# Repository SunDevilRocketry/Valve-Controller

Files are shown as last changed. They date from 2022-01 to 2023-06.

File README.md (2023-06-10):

<h1>Valve Controller</h1>

<p>PCB Revision: 3.1</p>
<p>PCB Part No: L0005</p>
<p>The liquid engine's valve controller (L0005) contains the processor responsible for managing valve actuation commands issued by the liquid engine controller (L0002). The board contains opto-isolated solid state relays for solenoid actuation and a Pulse Width Modulation interface for issuing stepper motor commands that initiate actuation of the liquid engine's main propellant valves. The board contains an STM32H7 ARM Cortex-M7 microcontroller for processing, programmed using an STLink/V2 with a 20-pin IDC cable connection. The board is powered from the 5V buck converter on L0002, which is also used to power the photogate sensors used for valve position calibration. In order to allow the controller to know the true actuation state of the solenoids even in the event of a power failure, the board contains an AC power supply monitoring circuit which produces an indication signal read by the MCU when AC power is available for solenoid actuation. </p>

<p><b>Working Directory Structure:</b></p>

<p>
   cad: 3d models

   doc: documentation

   img: images of circuit/footprints for github display 

   lib: libraries for schematic symbols and footprints

   production: files needed for pcb fabrication, e.g. gerbers, profile, drill file

   sim: simulation models/files 

   src: source design files, e.g. schematic and PCB layout files
</p>

<h2>3D Model: </h2>
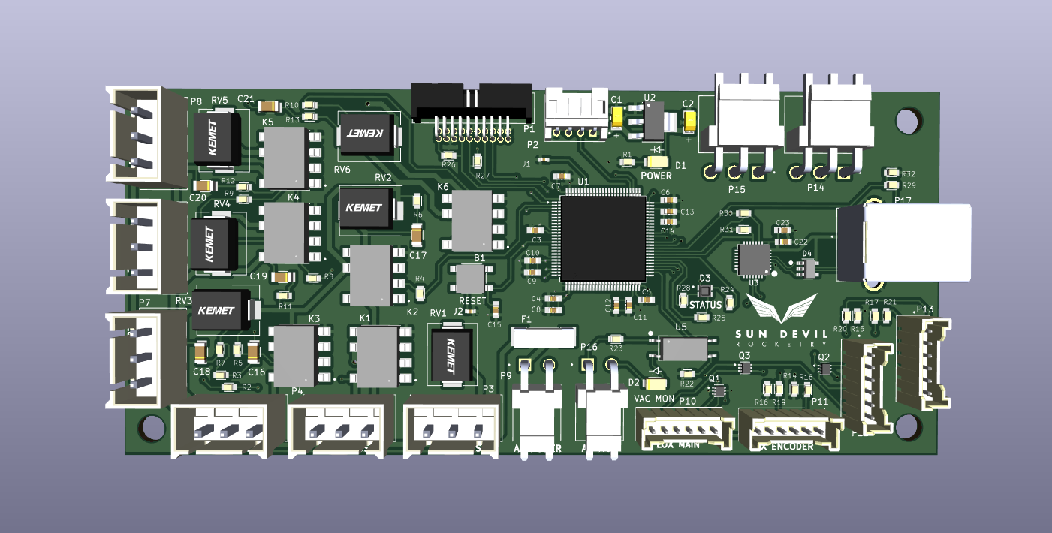
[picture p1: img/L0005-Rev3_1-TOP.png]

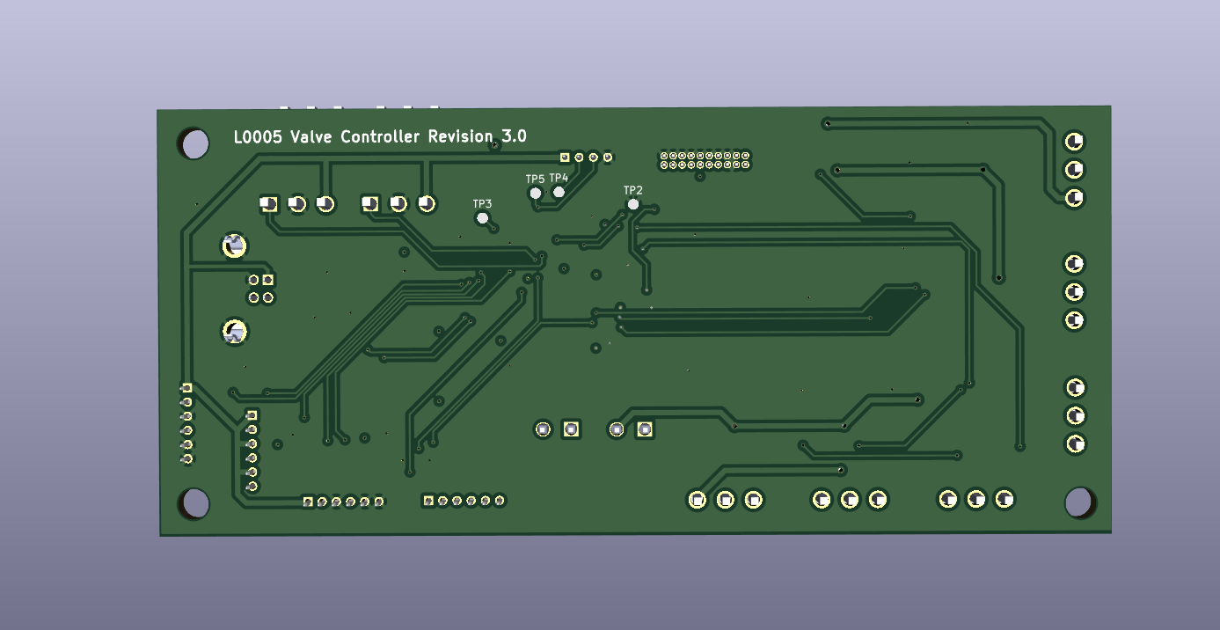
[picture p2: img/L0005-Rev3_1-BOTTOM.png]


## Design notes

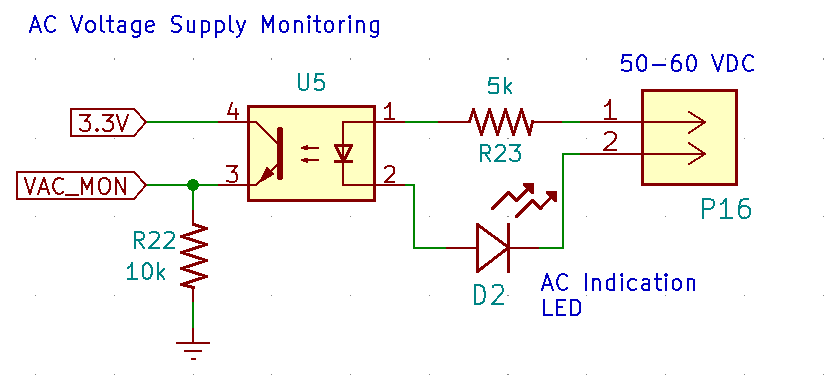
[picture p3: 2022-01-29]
img/AC-Supply-Monitoring-schematic.png

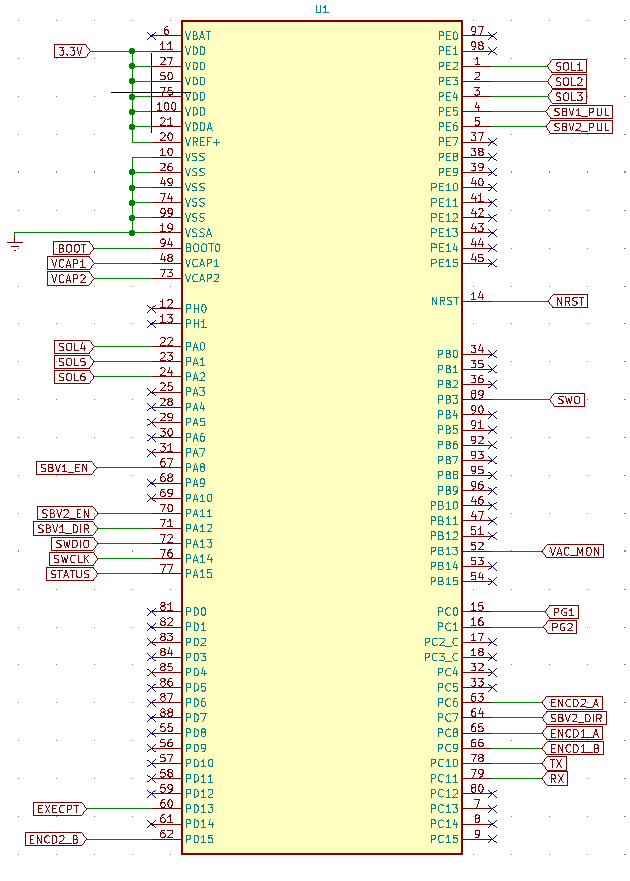
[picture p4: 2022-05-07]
img/MCU-schematic.png

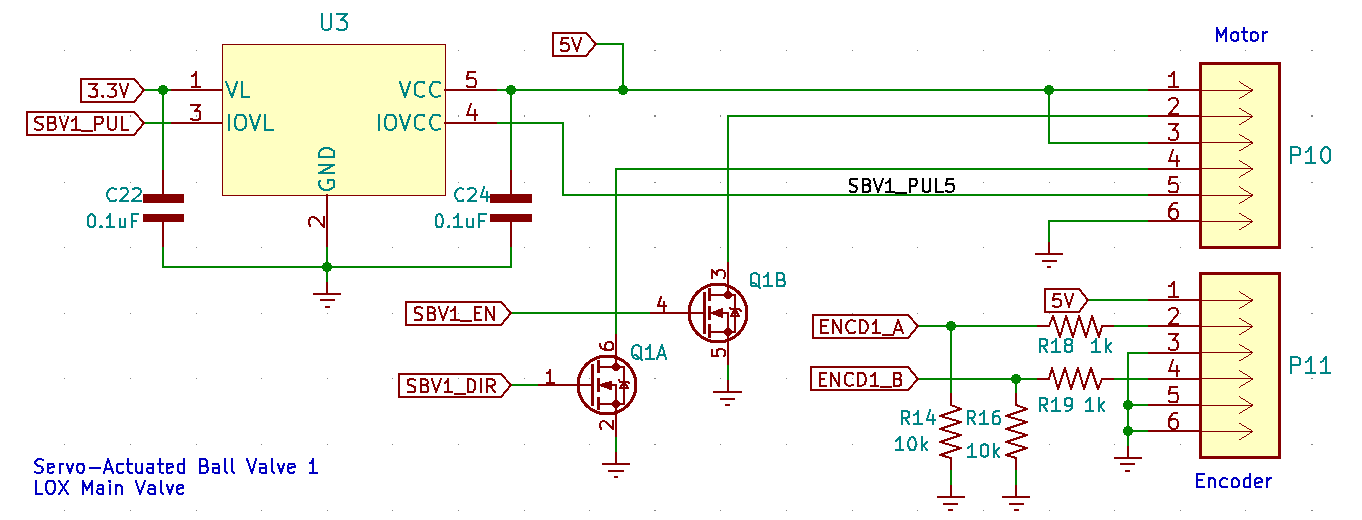
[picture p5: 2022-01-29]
img/Ball-Valve-Schematic.png

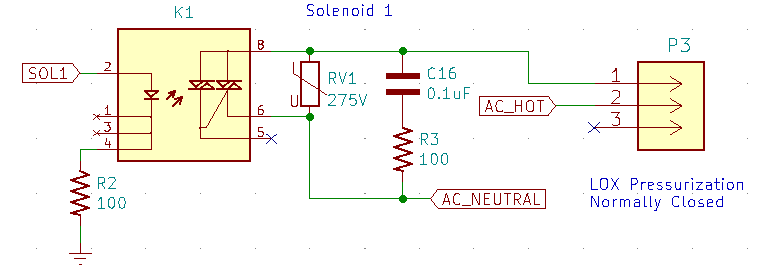
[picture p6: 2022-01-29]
img/Solenoid-schematic.png

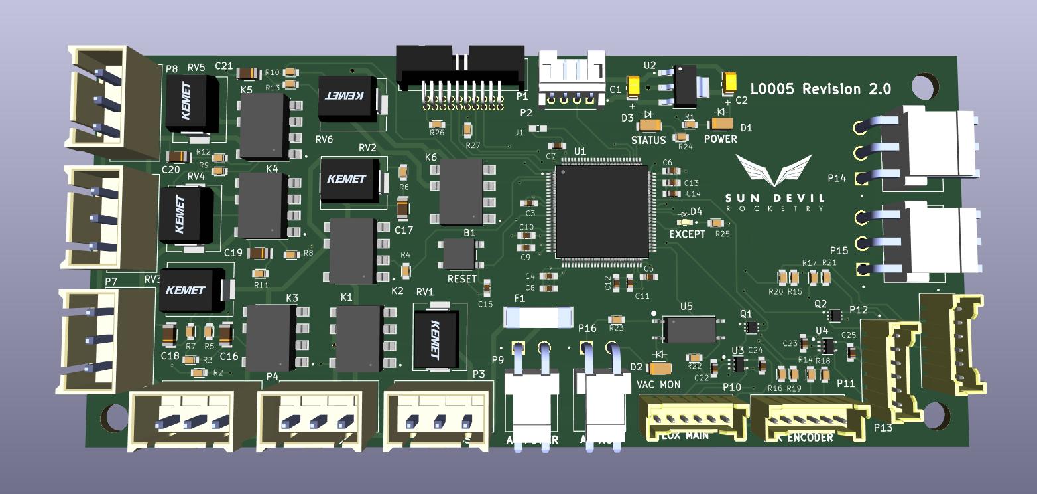
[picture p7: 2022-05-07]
img/L0005-Valve-Controller-FRONT.jpg

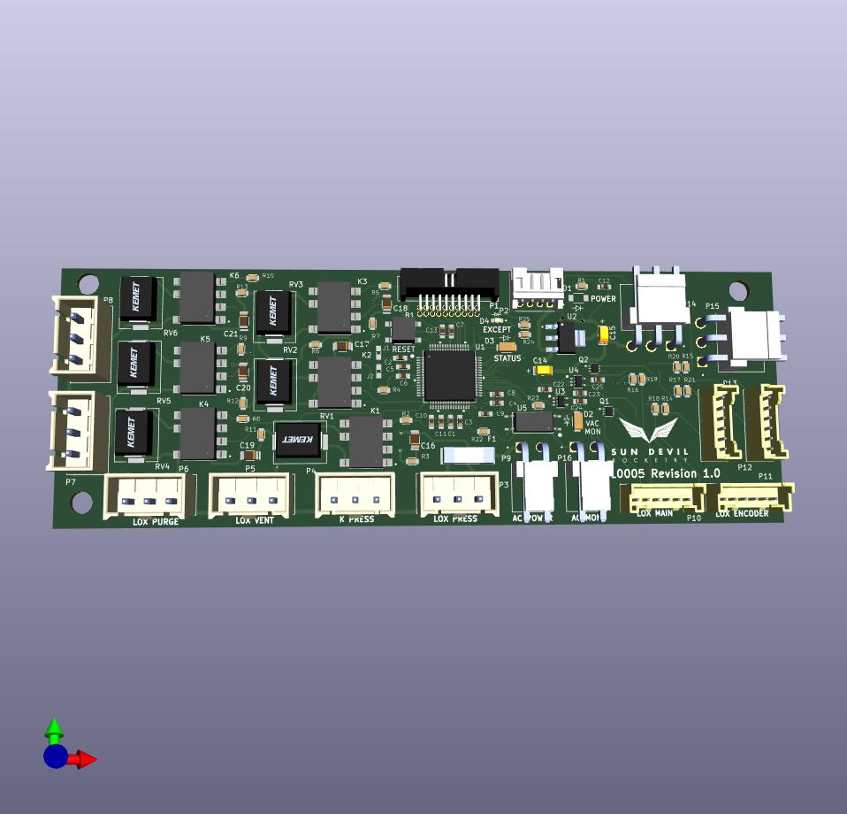
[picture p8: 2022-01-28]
img/L0005-Valve-Controller.jpg

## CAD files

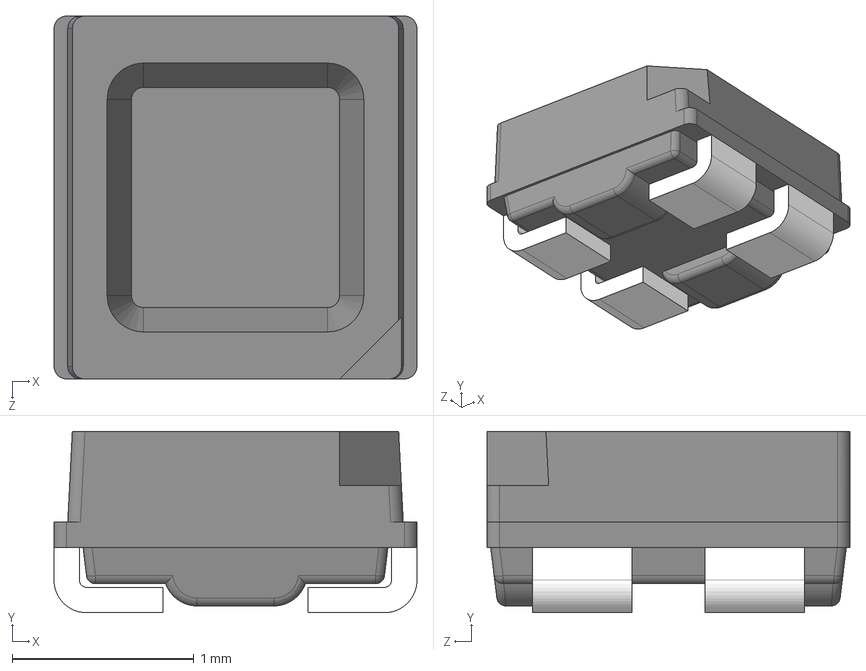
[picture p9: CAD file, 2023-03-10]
CAD/3Dfiles/CLMVC-FKA-CL1D1L71BB7C3C3.STEP
2.00 x 1 x 2.00 mm

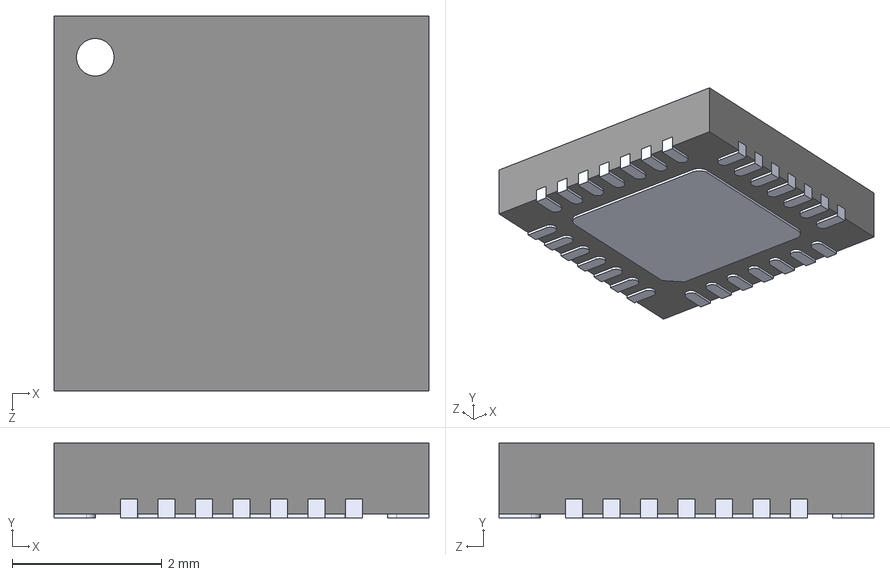
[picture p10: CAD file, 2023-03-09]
CAD/3Dfiles/CP2102-GMR_QFN28.step
5.00 x 1.00 x 5.00 mm

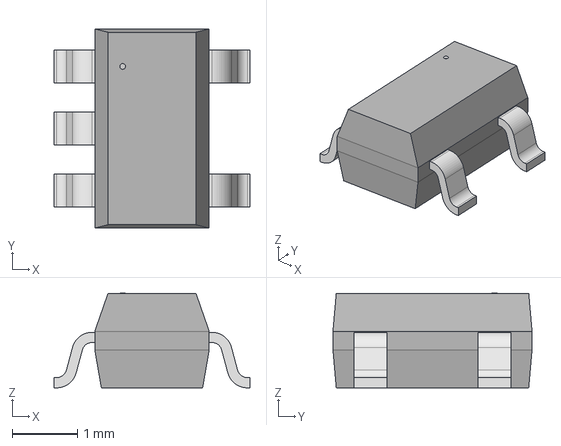
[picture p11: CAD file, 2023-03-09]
CAD/3Dfiles/SP0504BAHTG.step
3.00 x 3.05 x 1.45 mm

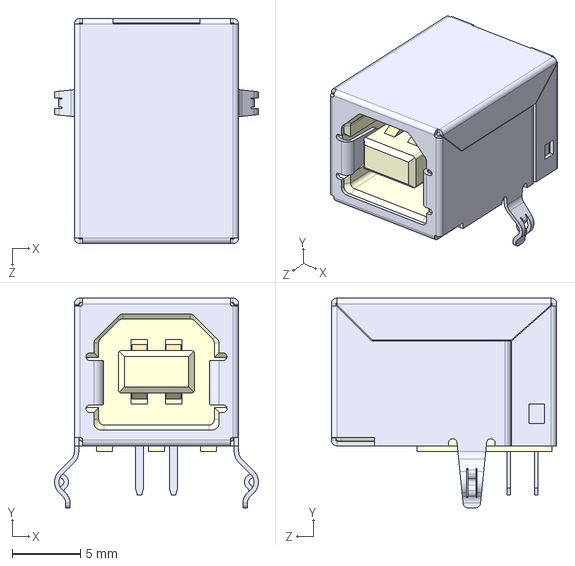
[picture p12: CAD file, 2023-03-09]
CAD/3Dfiles/SS-52300-001--3DModel-STEP-56544.STEP
14.9 x 15.4 x 16.5 mm

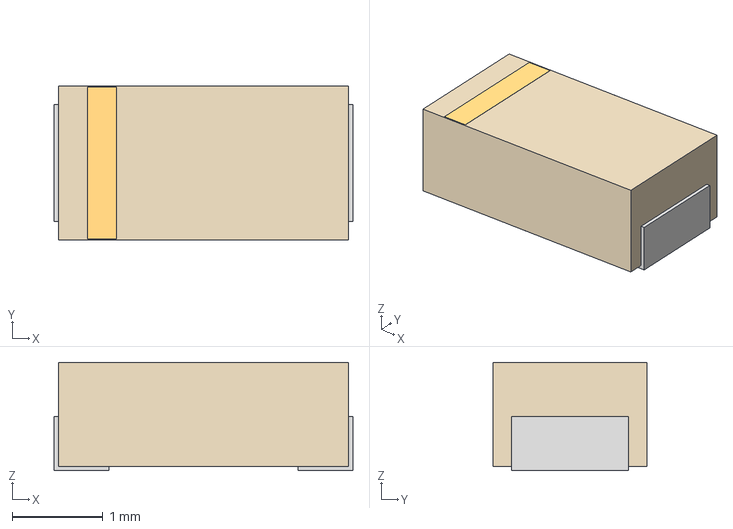
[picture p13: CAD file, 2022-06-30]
CAD/3Dfiles/SML-LX1206GC-TR.step
3.30 x 1.70 x 1.20 mm

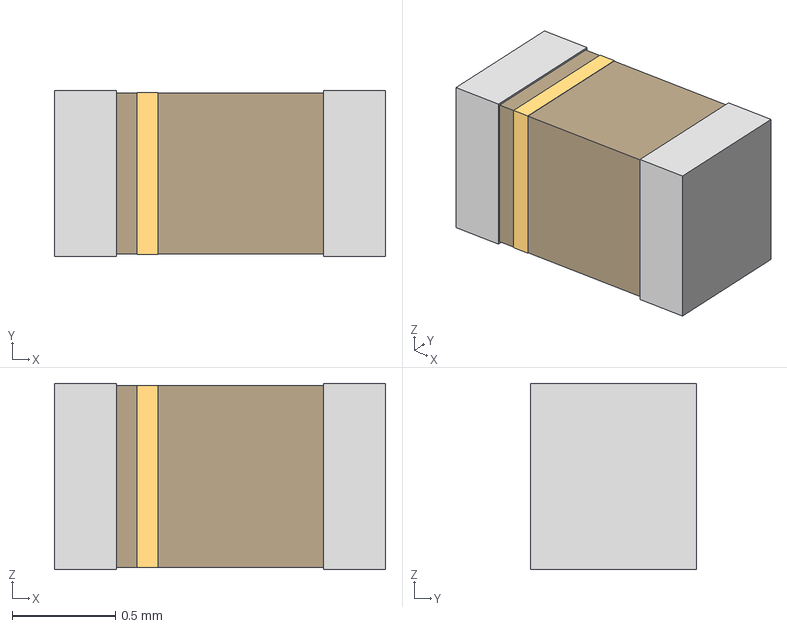
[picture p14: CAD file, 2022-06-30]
CAD/3Dfiles/CAP_0603.step
1.60 x 0.8 x 0.9 mm

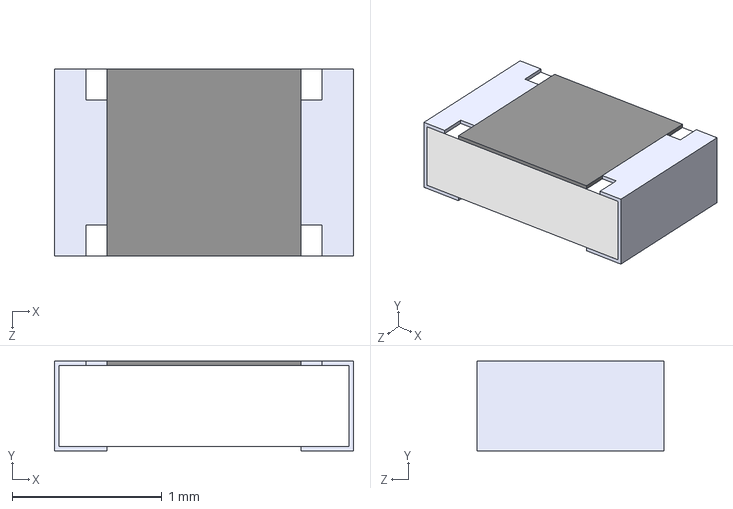
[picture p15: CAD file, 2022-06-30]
CAD/3Dfiles/RES_0805.step
2.00 x 0.6 x 1.25 mm

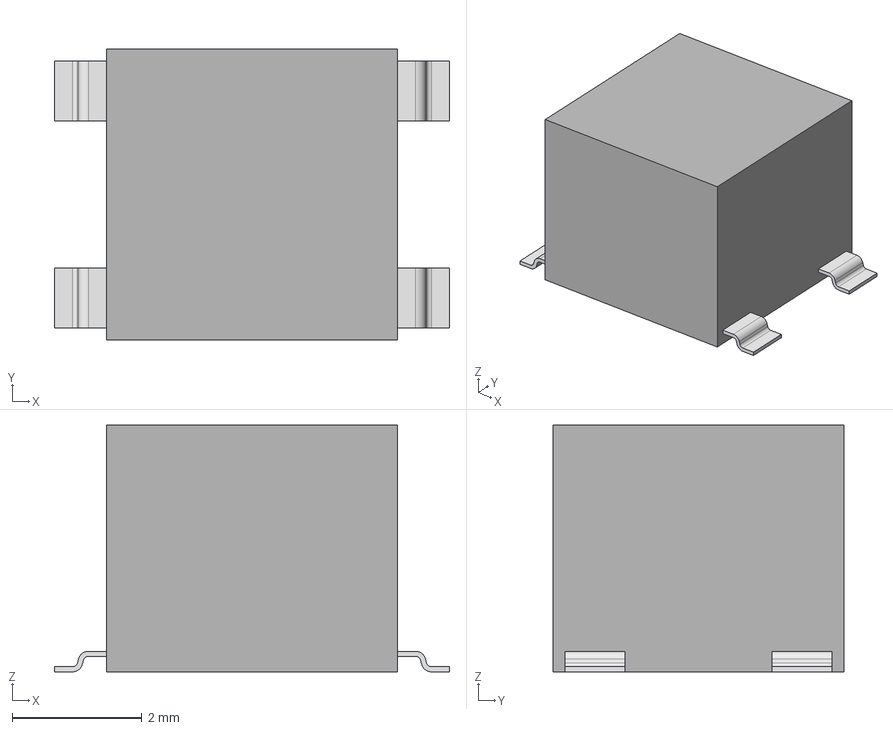
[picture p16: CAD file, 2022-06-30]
CAD/3Dfiles/PTS647SM38SMTR2LFS_CNK.step
6.10 x 4.50 x 3.81 mm

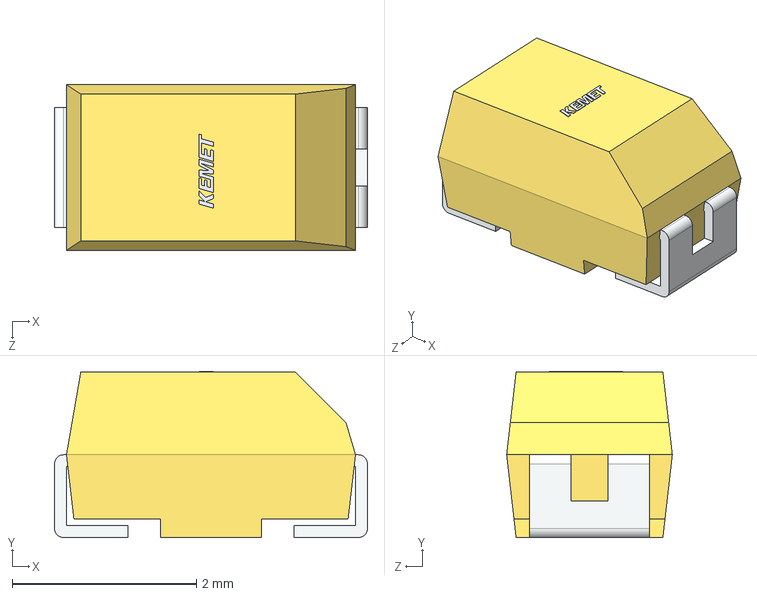
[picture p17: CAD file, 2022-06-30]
CAD/3Dfiles/T491A106K010AT.step
3.40 x 1.81 x 1.80 mm

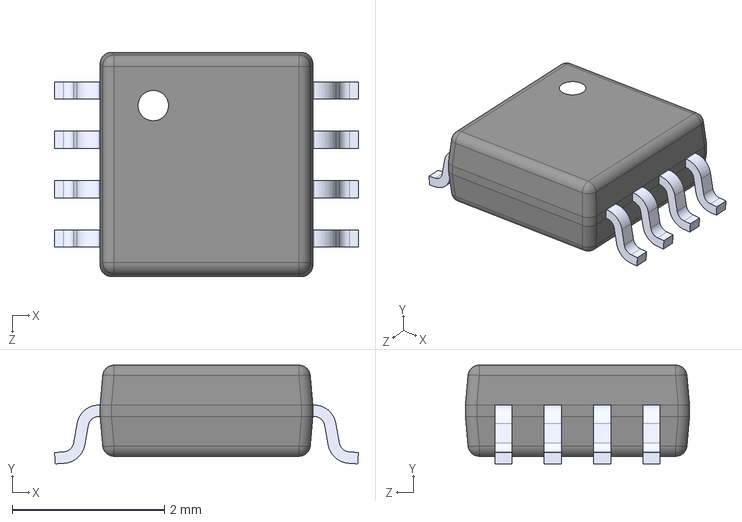
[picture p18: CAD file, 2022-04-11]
CAD/3Dfiles/SN74LVC1G139DCTR.STEP
4.00 x 1.30 x 2.95 mm

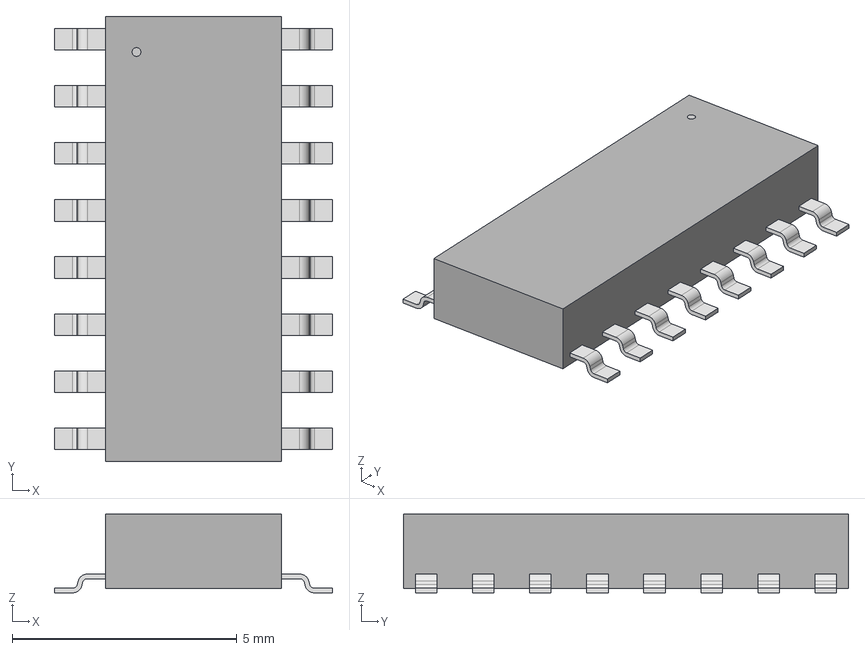
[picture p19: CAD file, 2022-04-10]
CAD/3Dfiles/MC74HCT138ADR2G.step
6.20 x 9.91 x 1.75 mm

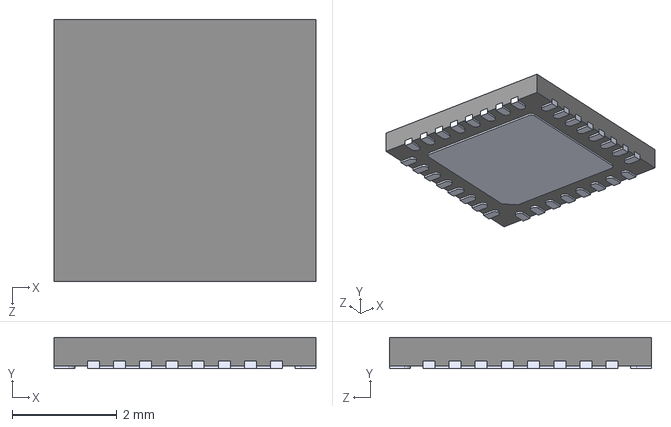
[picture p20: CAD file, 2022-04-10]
CAD/3Dfiles/STM32F334K8U6.step
5.00 x 0.6 x 5.00 mm

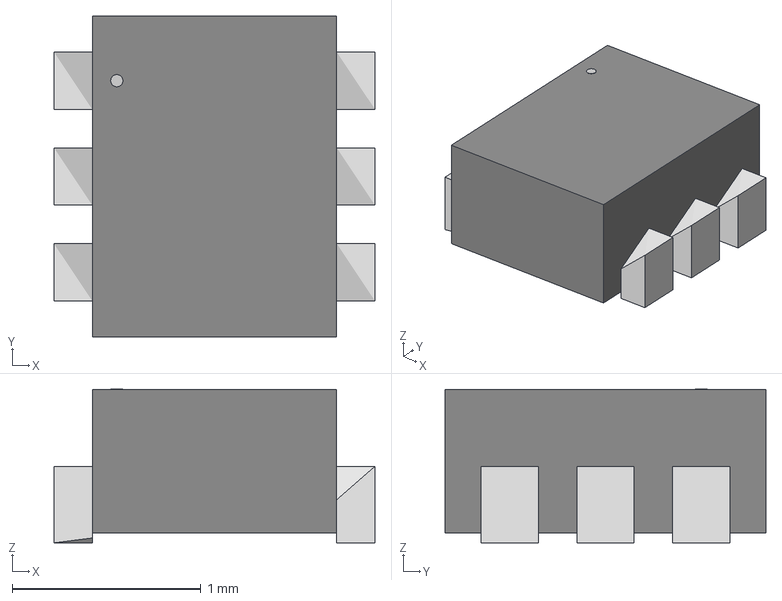
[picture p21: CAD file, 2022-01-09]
CAD/3Dfiles/CMLDM7003TR_BRN.step
1.70 x 1.70 x 0.815 mm

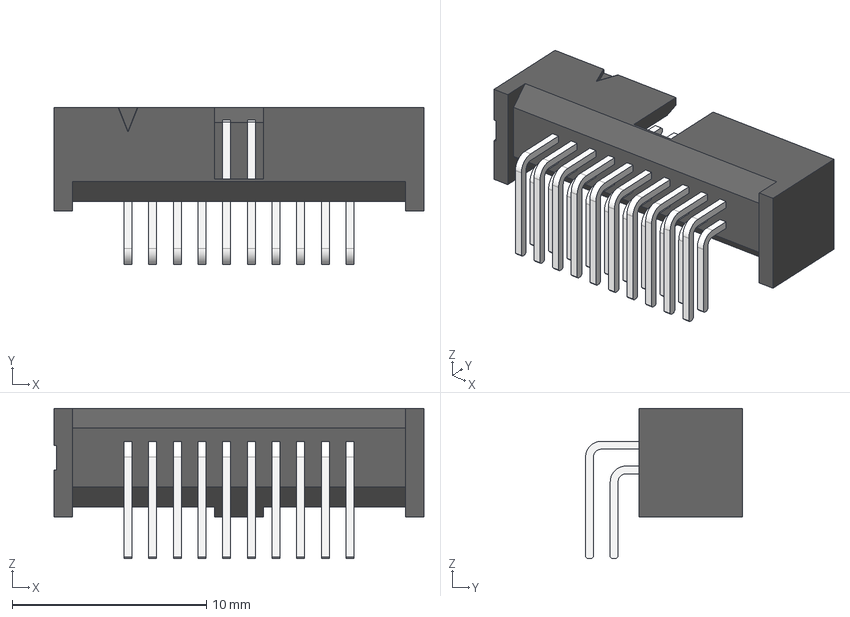
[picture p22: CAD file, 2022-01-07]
CAD/3Dfiles/3220-20-0200-00.stp
19.1 x 8.08 x 7.75 mm
_SHF-110-01-D_header
_SHF-First_Position_Indicator
_T-1S71-02-10-D-RA

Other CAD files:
CAD/3Dfiles/140-504-415-000.step
CAD/3Dfiles/test-140-504-415-000.step
CAD/3Dfiles/SML-D12U1WT86.step
CAD/3Dfiles/LQFP64_10X10_NXP.step
CAD/3Dfiles/0678L9100-02.step
CAD/3Dfiles/353130360.stp
CAD/3Dfiles/353620650.step
CAD/3Dfiles/51025-03-0100-01.step
CAD/3Dfiles/647676-2.step
CAD/3Dfiles/647676-3.stp
CAD/3Dfiles/AQH0223AX.step
CAD/3Dfiles/CAP_1206.step
CAD/3Dfiles/CWR11_C__KEM.step
CAD/3Dfiles/LMS8117AMP-3.3NOPB.STEP
CAD/3Dfiles/MAX3370EXK.step
CAD/3Dfiles/Opto_140105146000.step
CAD/3Dfiles/RES_0603.step
CAD/3Dfiles/STM32L151CCT6.step
CAD/3Dfiles/VP3225K401R250.step

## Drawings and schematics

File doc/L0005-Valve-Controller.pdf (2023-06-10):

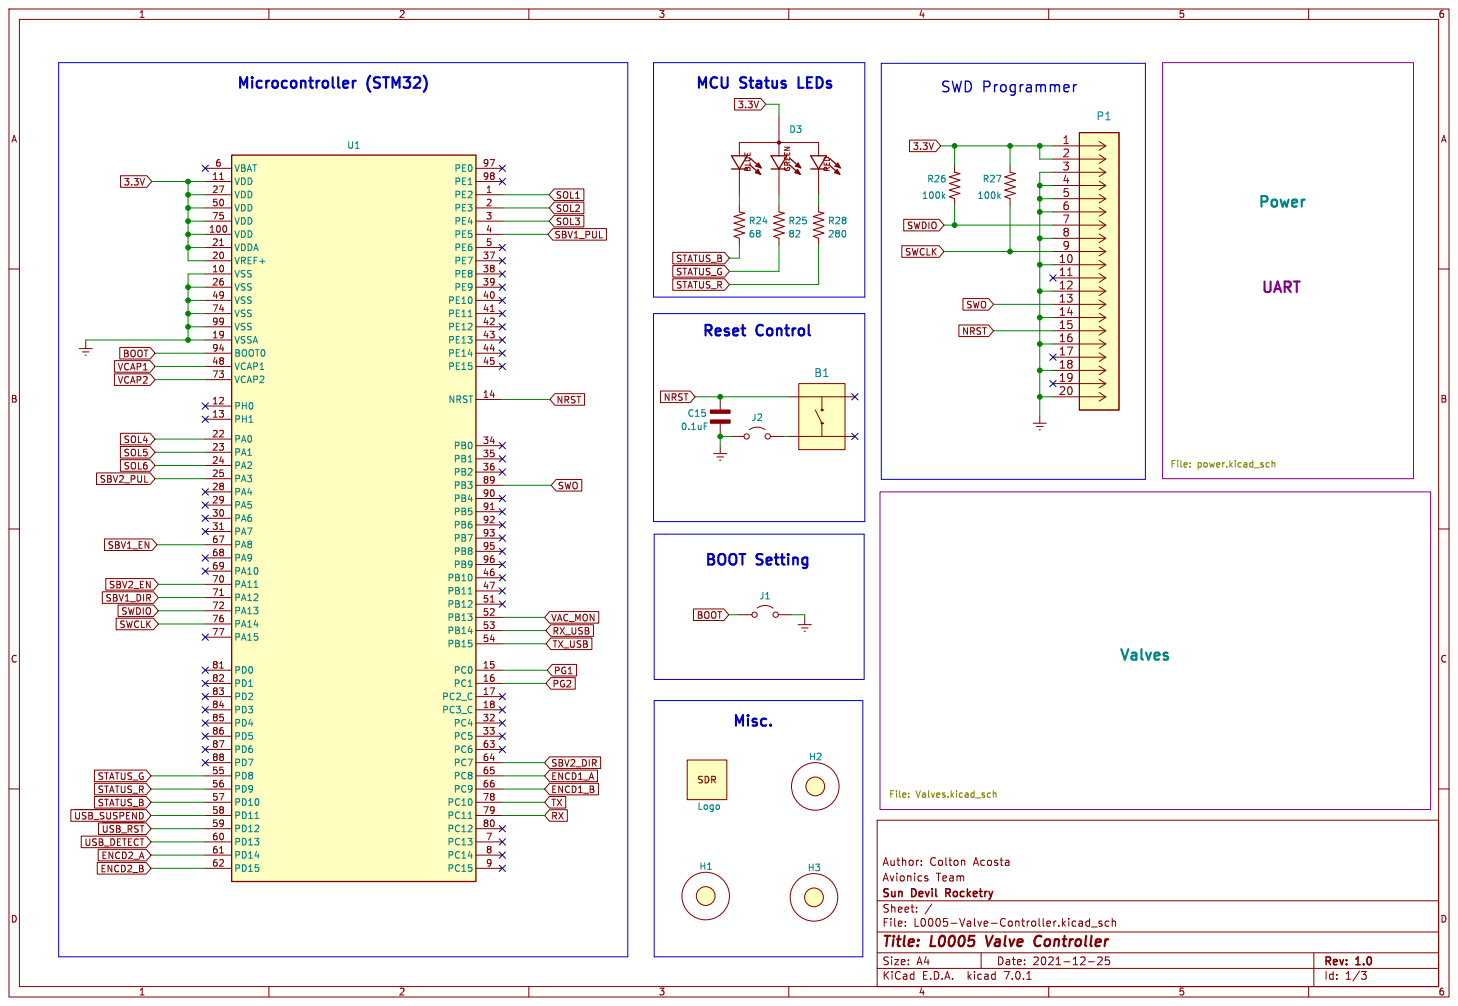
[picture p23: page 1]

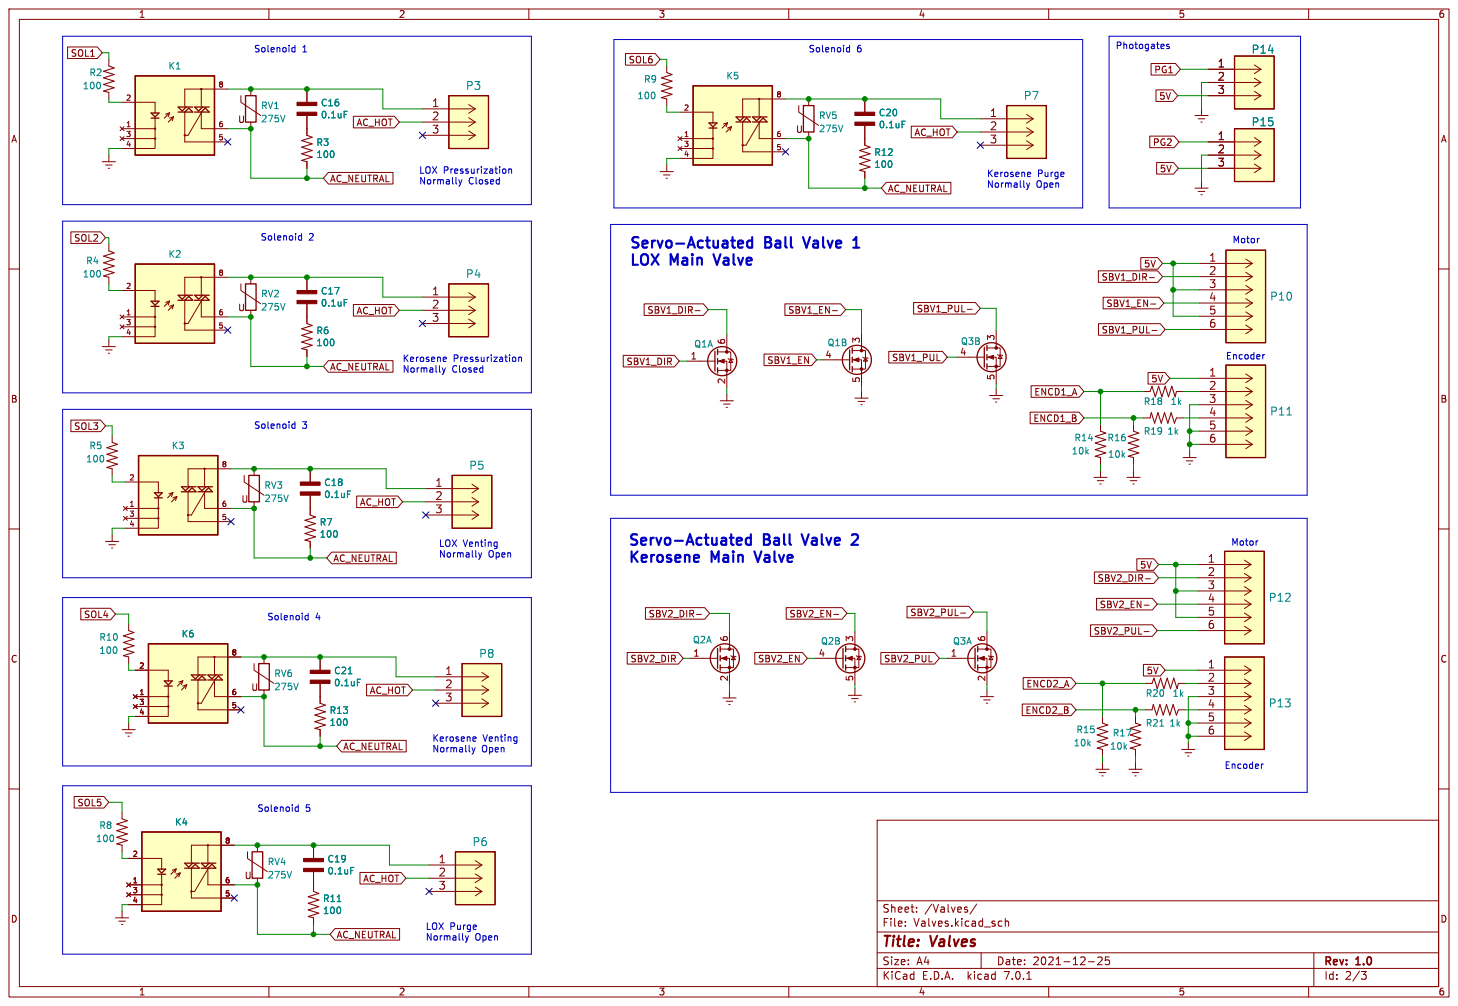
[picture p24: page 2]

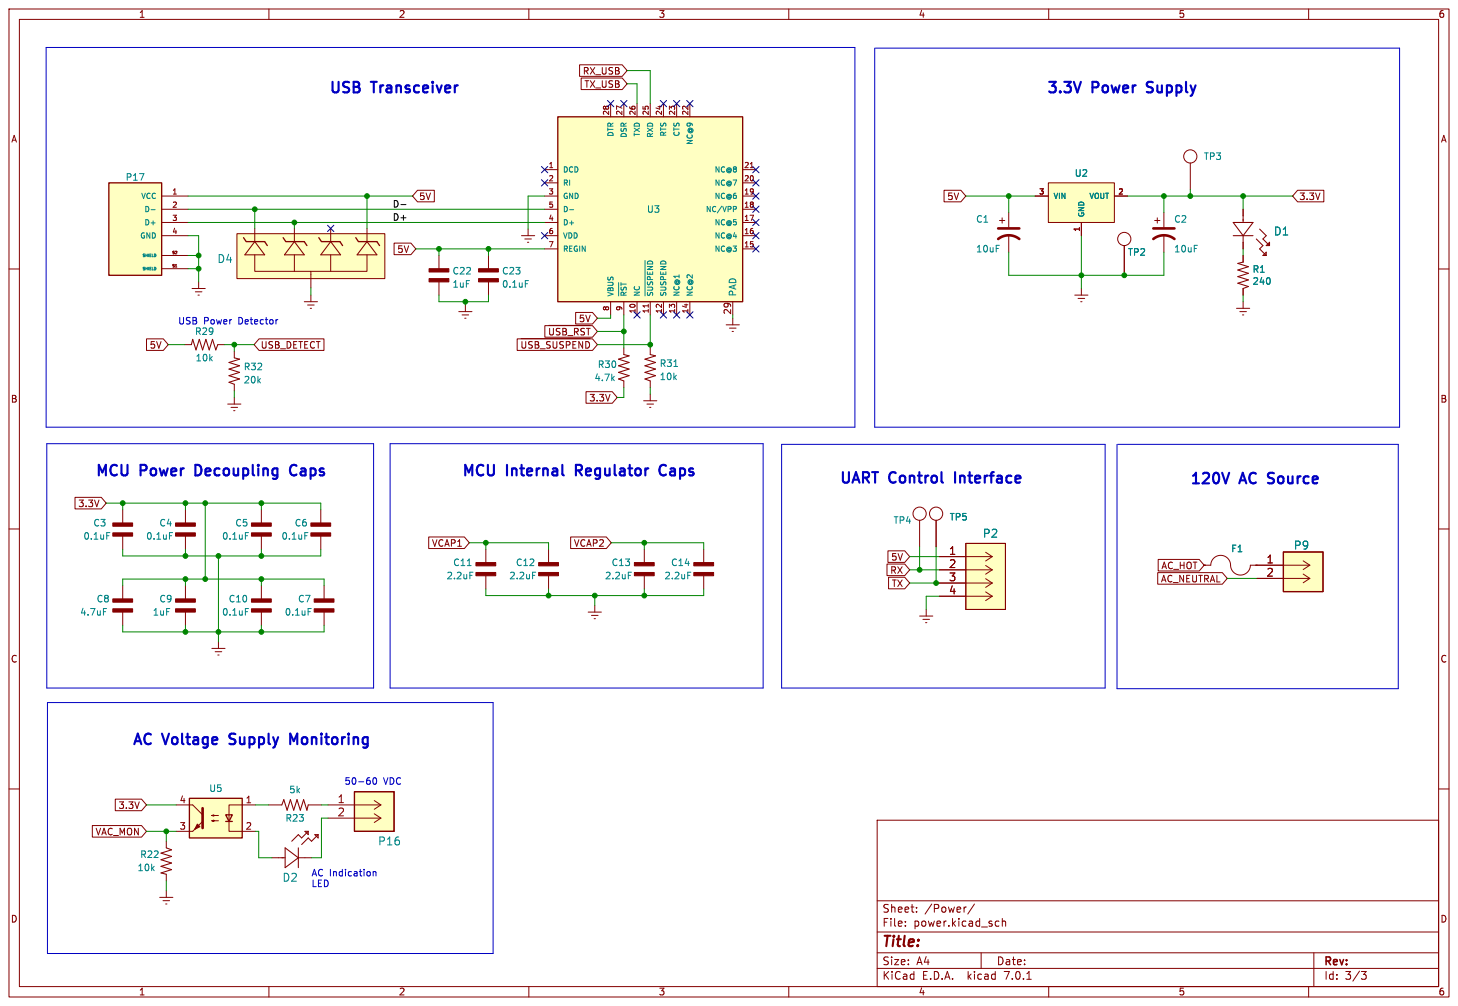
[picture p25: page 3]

LED MCU Power Decoupling Caps

MCU Internal Regulator Caps

AC Voltage Supply Monitoring

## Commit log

2021-12-15 Started lib files and added MCU
    [L0005-Valve-Controller.kicad_pcb, L0005-Valve-Controller.sch, STM32L151CCT6.step]
2021-12-18 Added SSR to lib files
    [AQH0223AX.step]
2021-12-18 Added 0603 resistor to lib files
    [RES_0603.step]
2021-12-18 Added 1206 capacitor to lib files
    [CAP_1206.step]
2021-12-18 Added varistor to lib files
    [VP3225K401R250.step]
2021-12-21 Added programming connector to lib files
    [3220-20-0200-00.stp]
2021-12-23 Added connectors to lib files
    [140-504-415-000.step, 51025-03-0100-01.step, CWR11_C__KEM.step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]
2021-12-23 Added optocoupler to lib files
    [353130360.stp, 353620650.step, 647676-2.step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]
2021-12-24 Added level shifter to lib files
    [MAX3370EXK.step]
2021-12-24 Added LED to lib files
2021-12-24 Added Button to lib files
2021-12-25 Added NXP MCU to lib files
    [LQFP64_10X10_NXP.step]
2021-12-25 Added MCU power decoupling to schematic
    [L0005-Valve-Controller.sch]
2021-12-26 Added programmer to schematic
    [L0005-Valve-Controller.sch]
2021-12-26 Added power supply to schematic
    [L0005-Valve-Controller.sch]
2021-12-26 Added UART interface to schematic
    [L0005-Valve-Controller.sch]
2021-12-26 Added SSR Solenoid drivers to schematic
    [L0005-Valve-Controller.sch, Solenoids.sch]
2021-12-26 Added AC source to schematic
    [L0005-Valve-Controller.sch, Solenoids.sch]
2021-12-26 Added servo-actuated ball valves to schematic
    [L0005-Valve-Controller.sch]
2021-12-26 Added fuse to lib files
    [0678L9100-02.step]
2021-12-27 added simulation for rectifier
    [Rectifier.kicad_pcb, Rectifier.sch]
2021-12-27 Added Red LED to lib files
    [Rectifier.sch, SML-D12U1WT86.step]
2021-12-28 Added MCU control signals
    [L0005-Valve-Controller.sch]
2021-12-28 Added test points
    [L0005-Valve-Controller.sch]
2021-12-28 routed MCU power decoupling
2021-12-28 routed solenoid SSRs
    [L0005-Valve-Controller.kicad_pcb, L0005-Valve-Controller.sch, Solenoids.sch]
2021-12-28 finished controller routing
    [L0005-Valve-Controller.kicad_pcb, Solenoids.sch]
2022-01-07 fixed SWD schematic connections for J-Link
    [140-504-415-000.step, 3220-20-0200-00.stp, 353130360.stp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]
2022-01-08 moved stepper circuits to second schematic sheet
    [L0005-Valve-Controller.kicad_sch, Solenoids.kicad_sch, Valves.kicad_sch]
2022-01-09 inverted VAC_MON signal
    [L0005-Valve-Controller.kicad_sch]
2022-01-09 wrote python script to calculate NMOS current
2022-01-09 Added NMOS array to lib files
    [CMLDM7003TR_BRN.step]
2022-01-09 Added 5V open drain logic to stepper motor control signals
    [L0005-Valve-Controller.kicad_sch, Valves.kicad_sch]
2022-01-09 Rearranged schematic
    [L0005-Valve-Controller.kicad_sch, Valves.kicad_sch]
2022-01-09 ploted schematic capture to pdf
    [L0005-Valve-Controller.kicad_sch]
2022-01-09 changed LED current limiters to 470 Ohm
    [L0005-Valve-Controller.kicad_sch]
2022-01-09 replotted schematic with updated LED resistor values
2022-01-10 rerouted PCB to include 5V logic MOSFETS
    [L0005-Valve-Controller.kicad_pcb, L0005-Valve-Controller.kicad_sch, Valves.kicad_sch]
2022-01-10 fixed kicad glitch
2022-01-10 produced gerbers files
    [L0005-Valve-Controller-B_Cu.gbr, L0005-Valve-Controller-B_Mask.gbr, L0005-Valve-Controller-B_Paste.gbr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]
2022-01-10 Fixed error with regulator routimg
    [L0005-Valve-Controller-B_Cu.gbr, L0005-Valve-Controller-B_Mask.gbr, L0005-Valve-Controller-B_Paste.gbr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]
2022-01-29 Corrected README detail regarding main valve actuation
2022-01-29 Added pcb part number info to readme
2022-01-29 added PCB image to README
2022-01-29 Added schematic images to readme
2022-01-29 replaced readme MCU schematic
2022-01-29 removed old readme schematic
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2022-04-10 added new STM32 MCU to lib files
    [L0005-Valve-Controller-B_Cu.gbr, L0005-Valve-Controller-B_Mask.gbr, L0005-Valve-Controller-B_Paste.gbr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]
2022-04-10 added decoder to lib files
    [MC74HCT138ADR2G.step]
2022-04-11 added solenoid control decoder
    [L0005-Valve-Controller.kicad_sch, Valves.kicad_sch]
2022-04-11 added 2:4 decoder to lib files
    [SN74LVC1G139DCTR.STEP]
2022-04-11 added STM32H7 MCU
    [L0005-Valve-Controller.kicad_sch, Valves.kicad_sch, power.kicad_sch]
2022-04-12 updated schematic with STM32H7 MCU
    [L0005-Valve-Controller.kicad_sch]
2022-04-12 plotted schematic to pdf
    [L0005-Valve-Controller.kicad_pcb, L0005-Valve-Controller.kicad_sch, power.kicad_sch]
2022-04-13 routed rev 2
    [L0005-Valve-Controller-B_Cu.gbr, L0005-Valve-Controller-B_Mask.gbr, L0005-Valve-Controller-B_Paste.gbr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]
2022-04-13 zipped rev2 gerbers
    [L0005-Valve-Controller-B_Cu.gbr, L0005-Valve-Controller-B_Mask.gbr, L0005-Valve-Controller-B_Paste.gbr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]
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2022-06-30 fixed 3D model paths
    [647676-3.stp, CAP_0603.step, L0005-Valve-Controller.kicad_pcb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]
2022-07-02 added 3D model for rev 2.0
    [L0005-Valve-Controller.kicad_pcb, L0005-Valve-Controller.kicad_sch, power.kicad_sch]
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2023-03-09 added NO jumper to MCU reset button
    [L0005-Valve-Controller.kicad_sch, Valves.kicad_sch, power.kicad_sch]
2023-03-09 changed level shifter to opendrain mosfet for pulse interface
    [L0005-Valve-Controller.kicad_sch, Valves.kicad_sch]
2023-03-09 added USB to lib files and schematic
    [CP2102-GMR_QFN28.step, SP0504BAHTG.step, SS-52300-001--3DModel-STEP-56544.STEP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]
2023-03-10 finalized schematic
    [CLMVC-FKA-CL1D1L71BB7C3C3.STEP, L0005-Valve-Controller.kicad_sch, Valves.kicad_sch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]
2023-03-10 routed rev3
    [L0005-Valve-Controller-B_Cu.gbr, L0005-Valve-Controller-B_Mask.gbr, L0005-Valve-Controller-B_Paste.gbr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]
2023-06-10 fixed photogate pinouts to allow for straight cable to photogate connector
    [L0005-Valve-Controller-B_Cu.gbr, L0005-Valve-Controller-B_Mask.gbr, L0005-Valve-Controller-B_Paste.gbr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]
